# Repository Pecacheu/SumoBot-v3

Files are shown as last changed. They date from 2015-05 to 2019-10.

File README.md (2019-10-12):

# SumoBot 3.0
Everything you need to build a SumoBot!

## Links:
1. Arduino Software at: www.arduino.cc/main/software
2. DCCduino USB-to-Serial chip driver: www.wch.cn/download/CH341SER_EXE.html
3. Mac OS X version: www.wch.cn/download/CH341SER_MAC_ZIP.html
4. Node JS: www.nodejs.org

After installing the DCCduino driver on Mac OS X 10.9 and higher, an extra terminal command may be necessary.
Open Terminal, enter **sudo nvram boot-args="kext-dev-mode=1"**, and hit return.

## SumoBot v3 Assembly Guide:
(Video guide coming soon!)
###### If you're using the acrylic (0.22in) version, determine if you want a cloudy robot or a clear robot. If it's the latter, peel the cloudy protector film off the pieces before use.

#### Side Pieces:
1. Press x-shape inserts onto servo shafts and screw down using black screw.
2. Squeeze black rubber spacers into upper 2 side slots on servo casing.
3. Insert servos into servo holes in side pieces, ensuring that they face in opposite directions.
4. Use 2 silver screws each to secure servos onto side pieces. Add rubber bands to wheels.
6. Attach wheels using 2 silver screws with black rubber spacers (or metal silver spacers) each.

#### Bottom Piece:
6. Screw caster wheel onto bottom piece using remaining 2 black screws. Ensure it's on the opposite side of the piece from the arrow.

#### Chassis Assembly:
7. Insert top and bottom pieces into one of the side pieces, ensuring that all arrows point towards the front of the robot, and are on the topside (for top and bottom pieces) or inner (for side pieces) face.
8. Add the other side piece to the assembly. It's arrow should also face inwards.
9. Screw Arduino onto top piece using final 2 silver screws. The front left and back right holes will work best with most Arduino boards.

#### Wiring:
###### /* TO BE CONTINUED */

#### Final Steps:
10. Push front bumper onto front of robot.
11. Insert Li-Ion battery. Connect battery terminals to power block.

When robot is not in use, disconnect positive wire from battery side. *(NOT from breadboard power block side!)*

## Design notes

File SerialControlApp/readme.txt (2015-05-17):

This is control software, written in Node.js, for the SumoBot Jr. It allows you to control the robot with your computer's keyboard.

In order to use this software, you will need to install Node.js on your computer. Node.js is a popular real time server-side scripting language, based on Google's JavaScript engine. To download your copy, head over to nodejs.org and press the big green install button.

To run this software after installing Node.js, simply open your computer's terminal application, 'cd' to this folder, and type in "node index.js".

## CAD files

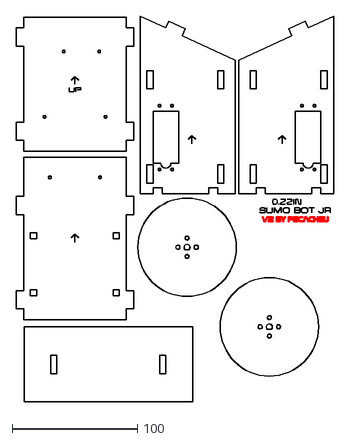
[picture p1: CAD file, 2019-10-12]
Laser Cut Files/0.22in-servos.dxf
253.4 x 307.7

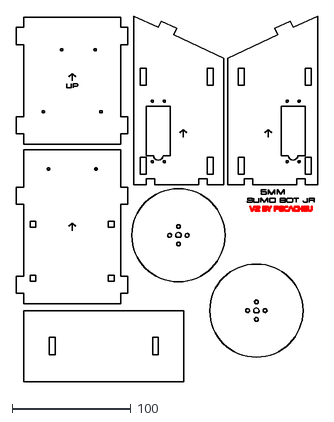
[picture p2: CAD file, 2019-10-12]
Laser Cut Files/5mm-servos.dxf
253.4 x 307.7

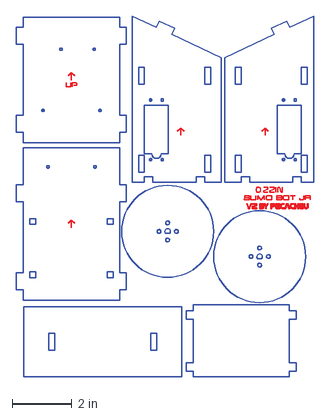
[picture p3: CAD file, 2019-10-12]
Laser Cut Files/sumobot-0.22in.dxf
9.98 x 12.1 in

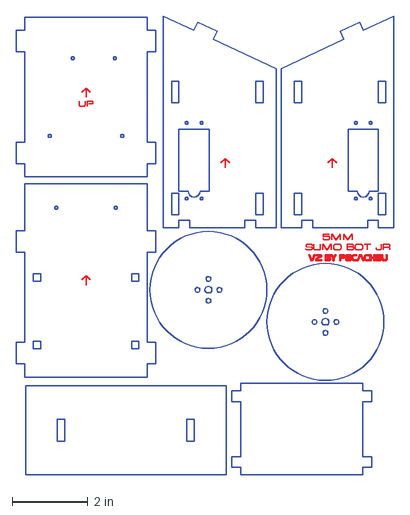
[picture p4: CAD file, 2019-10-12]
Laser Cut Files/sumobot-5mm.dxf
9.98 x 12.1 in

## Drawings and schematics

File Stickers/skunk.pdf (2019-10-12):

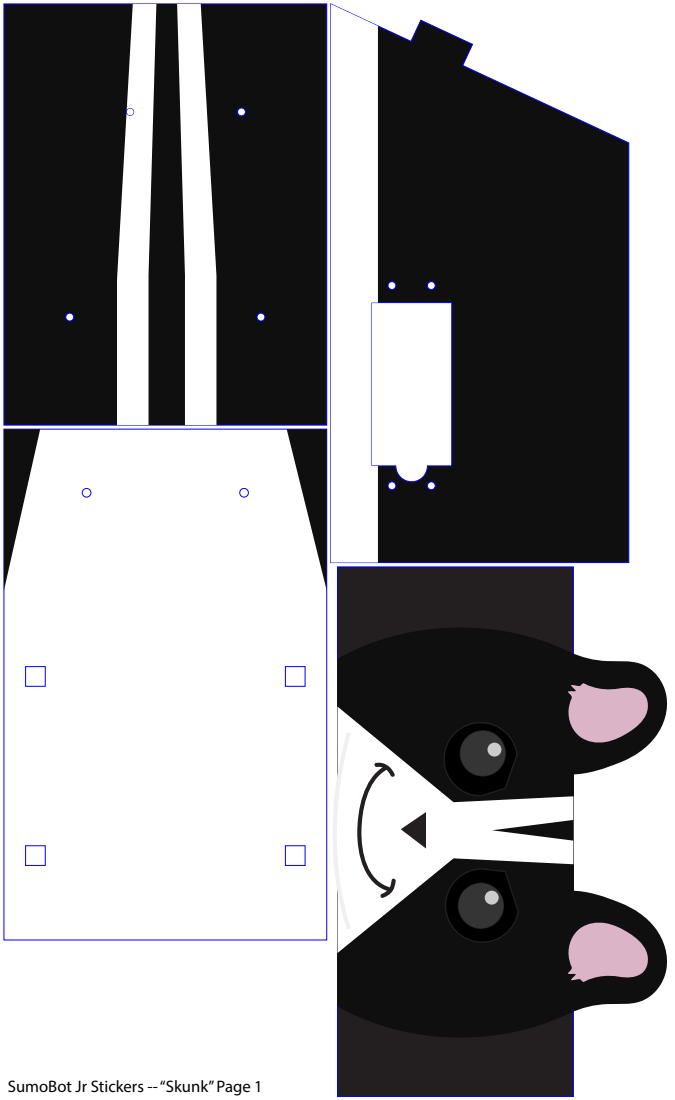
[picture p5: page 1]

SumoBot Jr Stickers -- “Skunk” Page 1

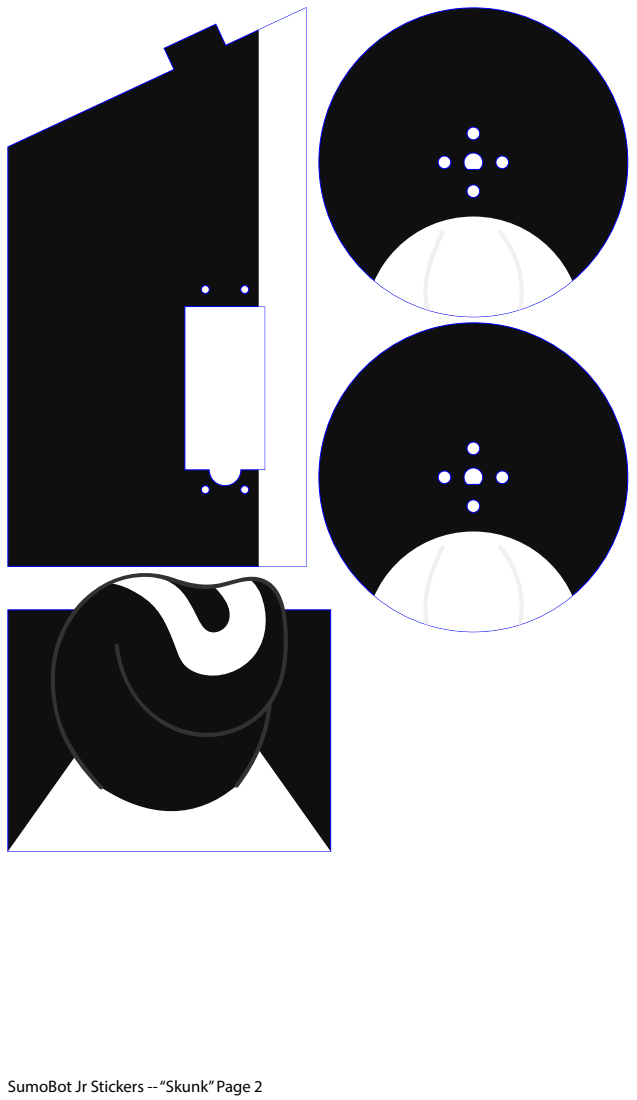
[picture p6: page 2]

SumoBot Jr Stickers -- “Skunk” Page 2

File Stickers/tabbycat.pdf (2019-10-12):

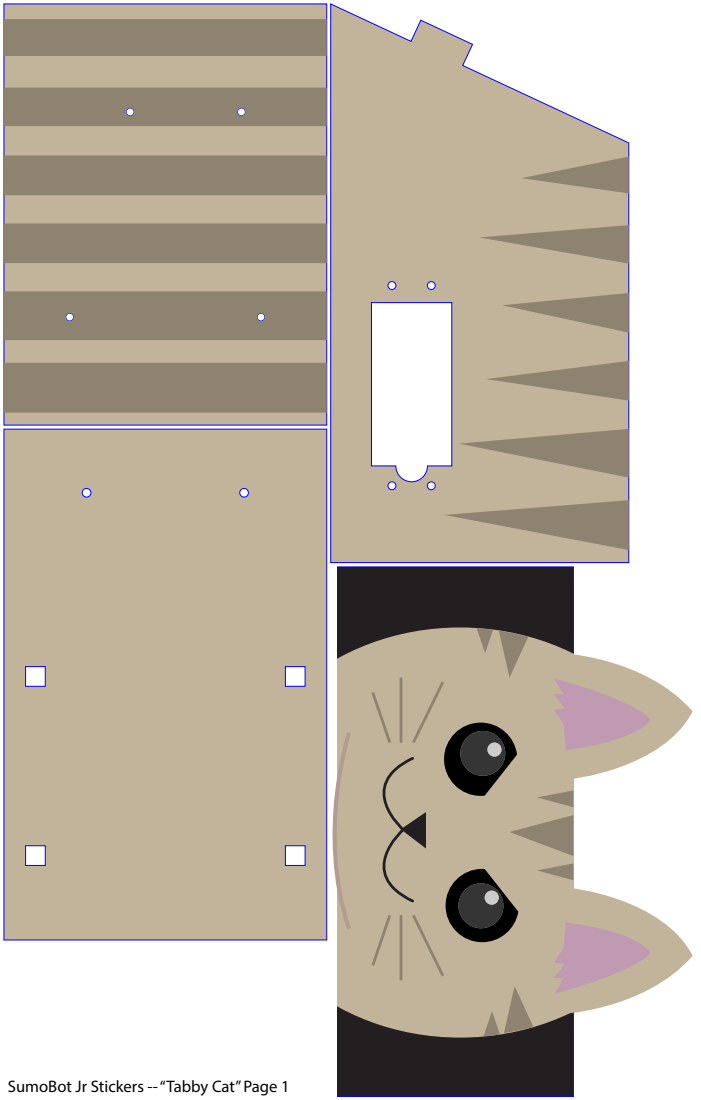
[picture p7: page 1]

SumoBot Jr Stickers -- “Tabby Cat” Page 1

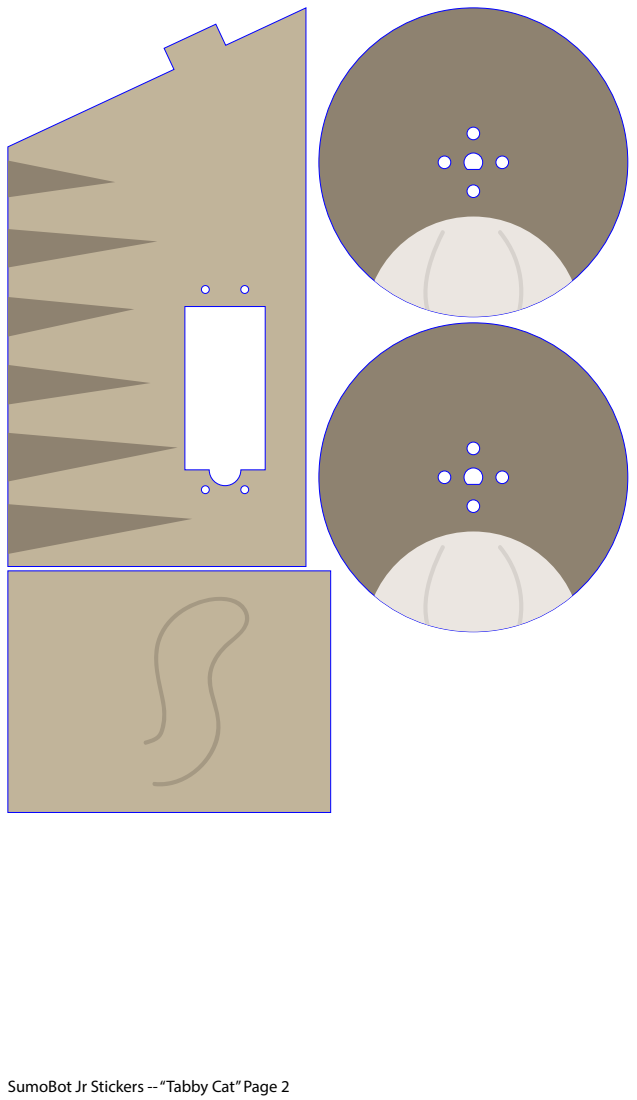
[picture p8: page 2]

SumoBot Jr Stickers -- “Tabby Cat” Page 2

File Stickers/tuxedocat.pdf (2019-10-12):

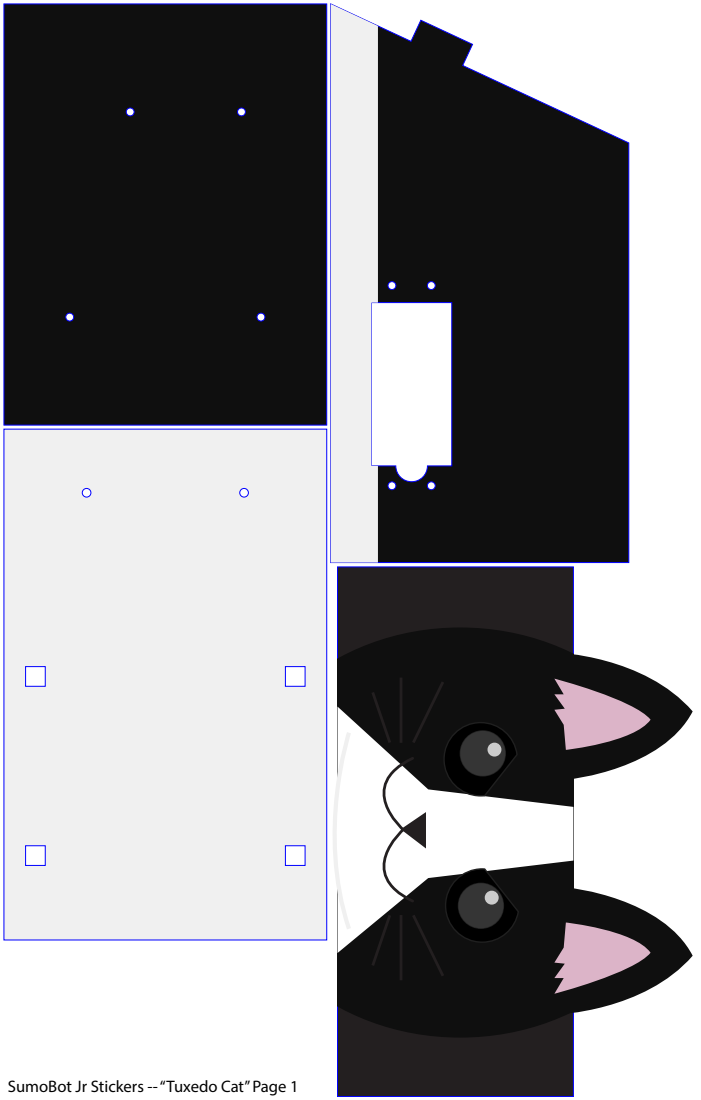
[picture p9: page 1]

SumoBot Jr Stickers -- “Tuxedo Cat” Page 1

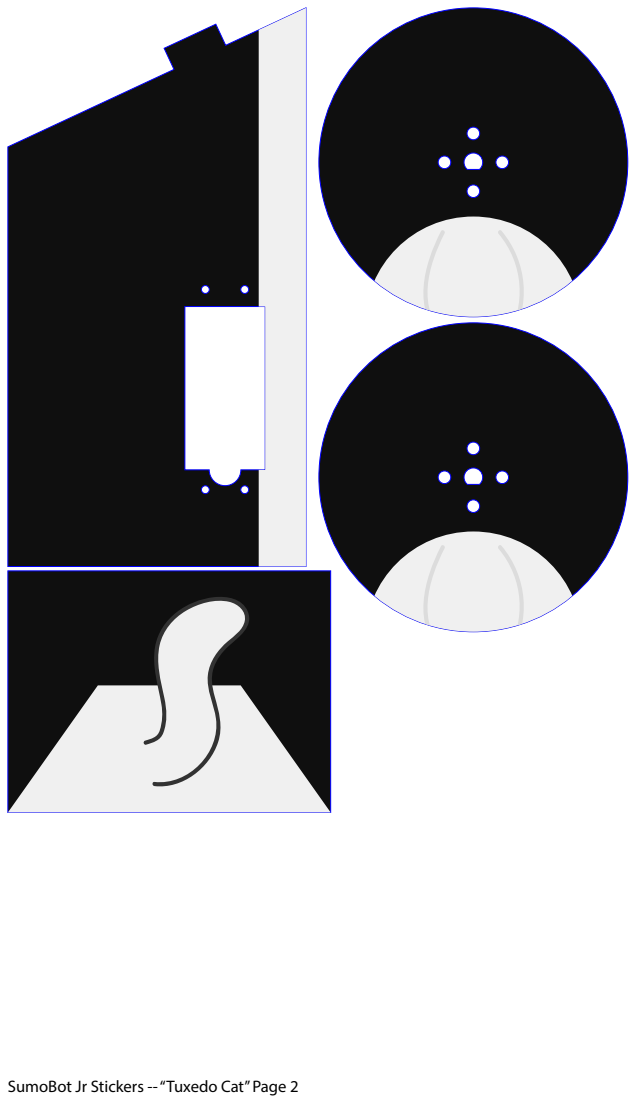
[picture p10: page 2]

SumoBot Jr Stickers -- “Tuxedo Cat” Page 2

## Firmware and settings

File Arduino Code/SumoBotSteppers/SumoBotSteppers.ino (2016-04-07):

//<legalstuff> This work is licensed under a GNU General Public License, v3.0. Visit http://gnu.org/licenses/gpl-3.0-standalone.html for details. </legalstuff>
//SumoBot v3 USB Link (Stepper Version). Copyright (©) 2016, Bryce Peterson (Nickname: Pecacheu, Email: Pecacheu@gmail.com)

//avr-libc library includes:
#include <avr/io.h>
#include <avr/interrupt.h>

#define NUM_MOTORS 2
#define STATUS_LED 13

//Pin Numbers:
#define DIR_1  6
#define STEP_1 5
#define SLP_1  4

#define CONFIG1_M0 3
#define CONFIG1_M1 2

#define DIR_2  10
#define STEP_2 11
#define SLP_2  12

#define CONFIG2_M0 9
#define CONFIG2_M1 8

//Globals: (Don't touch these!)
int savedStepMode = 1;
boolean savedBrakeStates[2] = {true, true};
volatile unsigned int motorPins[2] = {STEP_1, STEP_2};
volatile unsigned int driveMotorSpeed[2] = {0, 0};
volatile unsigned int driveMotorCount[2] = {0, 0};

void setup() {
  //Setup Pins:
  pinMode(STATUS_LED, OUTPUT);
  pinMode(STEP_1, OUTPUT);
  pinMode(DIR_1,  OUTPUT);
  pinMode(SLP_1, OUTPUT);
  digitalWrite(SLP_1, HIGH);
  pinMode(STEP_2, OUTPUT);
  pinMode(DIR_2,  OUTPUT);
  pinMode(SLP_2, OUTPUT);
  digitalWrite(SLP_2, HIGH);
  pinMode(CONFIG1_M0, OUTPUT);
  pinMode(CONFIG1_M1, OUTPUT);
  pinMode(CONFIG2_M0, OUTPUT);
  pinMode(CONFIG2_M1, OUTPUT);
  setStepMode(1); //Set Drivers to Full-Step Mode
  //Init Serial Comm:
  Serial.begin(9600); delay(500);
  //Setup Timer1:
  int timerScale = 1024; int clockSpeed_MHz = 16; int miliSeconds = 1;
  cli(); //Disable Global Interrupts
  TCCR1A = 0; TCCR1B = 0; //Set Entire TCCR1 Register to 0
  TCCR1B |= (1 << CS10); TCCR1B |= (1 << CS12); //Set to 1024 Scale Mode
  //Do The Math:
  double clockPeriod = clockSpeed_MHz*pow(10, 3) / timerScale;
  unsigned int timerCounts = (miliSeconds * clockPeriod) - 1;
  OCR1A = timerCounts; //Set Compare-Match Register to Desired Timer Count
  TCCR1B |= (1 << WGM12); //Turn on CTC Mode
  TIMSK1 |= (1 << OCIE1A); //Enable Timer Compare Interrupt
  sei(); //Enable Global Interrupts
}

void loop() {
  String msg = ""; boolean msgDone = false;
  while(1) {
    //Read New Commands From Serial:
    while(Serial.available() > 0) {
      char newChar = Serial.read();
      //Serial.print((unsigned char)newChar); Serial.print(" = '"); Serial.write(newChar); Serial.println("'"); //<< DEBUG
      if(newChar == '\n') { msgDone = true; break; }
      else msg += newChar;
    }
    
    //Process Next Command:
    if(msgDone && msg.length() >= 1) {
      Serial.print("Data: [");
      for(int i=0; i<msg.length(); i++) { if(i > 0) Serial.print(", "); Serial.print((unsigned char)msg[i]); }
      Serial.print("], Event Type: ");
      if(msg[0] == 'K' && msg.length() == 3) { //Key Update Event:
        Serial.println("Key Update");
        char LEFT = msg[1]; char RIGHT = msg[2];
        if(LEFT == 0) {
          driveMotor(2, false, 1, false);
        } else if(LEFT > 0) {
          driveMotor(2, true, -(abs(LEFT)*2)+256, false);
        } else {
          driveMotor(2, true, -(abs(LEFT)*2)+256, true);
        }
        if(RIGHT == 0) {
          driveMotor(1, false, 1, false);
        } else if(RIGHT > 0) {
          driveMotor(1, true, -(abs(RIGHT)*2)+256, true);
        } else {
          driveMotor(1, true, -(abs(RIGHT)*2)+256, false);
        }
      } else { //Unknown Event:
        Serial.println("Unknown");
      }
    }
    
    //Clear Processed Message Data:
    if(msgDone) { msg = ""; msgDone = false; }
  }
}

//An Exclusive-Or Function:
boolean XOR(boolean a, boolean b) {
  return a != b;
}

//Motor Control Functions:
void driveMotor(unsigned int motorNum, boolean startStop, unsigned char motorSpeed, boolean dir) {
  int STEP_PIN; int DIR_PIN;
  if(motorNum == 1) { STEP_PIN = STEP_1; DIR_PIN = DIR_1; } 
  else if(motorNum == 2) { STEP_PIN = STEP_2; DIR_PIN = DIR_2; }
  else return;
  if(startStop && motorSpeed > 0) {
    engageMotor(motorNum);
    digitalWrite(DIR_PIN, dir);
    int updateDelay = -(motorSpeed/4)+64;
    driveMotorSpeed[motorNum-1] = updateDelay;
  } else {
    driveMotorSpeed[motorNum-1] = 0;
    driveMotorCount[motorNum-1] = 0;
  }
}

void stepMotor(unsigned int motorNum, unsigned int steps, boolean dir) {
  int STEP_PIN; int DIR_PIN;
  if(motorNum == 1) { STEP_PIN = STEP_1; DIR_PIN = DIR_1; } 
  else if(motorNum == 2) { STEP_PIN = STEP_2; DIR_PIN = DIR_2; }
  else return;
  engageMotor(motorNum);
  digitalWrite(DIR_PIN, dir);
  for(int stp=0; stp<steps; stp++) {
    digitalWrite(STEP_PIN, HIGH);
    delay(5);
    digitalWrite(STEP_PIN, LOW);
    delay(5);
  }
}

void disengageMotor(unsigned int motorNum) {
  int SLP_PIN;
  if(motorNum == 1) { SLP_PIN = SLP_1; } 
  else if(motorNum == 2) { SLP_PIN = SLP_2; }
  else return;
  if(savedBrakeStates[motorNum-1]) {
    digitalWrite(SLP_PIN, LOW);
    //pinMode(SLP_PIN, INPUT);
    savedBrakeStates[motorNum-1] = false;
  }
}

void engageMotor(unsigned int motorNum) {
  int SLP_PIN;
  if(motorNum == 1) { SLP_PIN = SLP_1; } 
  else if(motorNum == 2) { SLP_PIN = SLP_2; }
  else return;
  if(!savedBrakeStates[motorNum-1]) {
    //pinMode(SLP_PIN, OUTPUT);
    digitalWrite(SLP_PIN, HIGH);
    savedBrakeStates[motorNum-1] = true;
  }
}

//Step Modes for Pololu LV (White) Stepper Driver:
//1  == Full Step
//2  == Half Step
//8  == Eighth Step
//16 == Sixteenth Step
void setStepMode(int stepMode) {
  switch(stepMode) {
    case 2:
      digitalWrite(CONFIG1_M0, HIGH);
      digitalWrite(CONFIG1_M1, LOW);
      digitalWrite(CONFIG2_M0, HIGH);
      digitalWrite(CONFIG2_M1, LOW);
      savedStepMode = 2;
    break;
    case 8:
      digitalWrite(CONFIG1_M0, LOW);
      digitalWrite(CONFIG1_M1, HIGH);
      digitalWrite(CONFIG2_M0, LOW);
      digitalWrite(CONFIG2_M1, HIGH);
      savedStepMode = 8;
    break;
    case 16:
      digitalWrite(CONFIG1_M0, HIGH);
      digitalWrite(CONFIG1_M1, HIGH);
      digitalWrite(CONFIG2_M0, HIGH);
      digitalWrite(CONFIG2_M1, HIGH);
      savedStepMode = 16;
    break;
    default:
      digitalWrite(CONFIG1_M0, LOW);
      digitalWrite(CONFIG1_M1, LOW);
      digitalWrite(CONFIG2_M0, LOW);
      digitalWrite(CONFIG2_M1, LOW);
      savedStepMode = 1;
  }
}

ISR(TIMER1_COMPA_vect) {
  for(int i=0; i<NUM_MOTORS; i++) { if(driveMotorSpeed[i]) {
    driveMotorCount[i]++;
    if(driveMotorCount[i] >= driveMotorSpeed[i]) {
      driveMotorCount[i] = 0;
      digitalWrite(motorPins[i], HIGH);
      delayMicroseconds(100);
      digitalWrite(motorPins[i], LOW);
    }
  }}
}

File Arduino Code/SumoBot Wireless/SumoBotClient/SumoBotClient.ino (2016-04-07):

//<legalstuff> This work is licensed under a GNU General Public License, v3.0. Visit http://gnu.org/licenses/gpl-3.0-standalone.html for details. </legalstuff>
//SumoBot v3 Wireless Client. Copyright (©) 2016, Bryce Peterson (Nickname: Pecacheu, Email: Pecacheu@gmail.com)

#include <Servo.h>
#include "RF24.h"

//#define NUM_MOTORS 2
#define STATUS_LED 13

//Pin Numbers:
#define MOTORL 2
#define MOTORR 3

#define MIN_PULSE 900
#define MAX_PULSE 2100

//Communication channel name:
byte CH[6] = "Node1";

//Globals: (Don't touch these!)
Servo MotorL; Servo MotorR;
RF24 radio(8,9);

void setup() {
  //Setup Pins & Motors:
  pinMode(STATUS_LED, OUTPUT);
  MotorL.attach(MOTORL); MotorR.attach(MOTORR);
  driveMotor(1, 128); driveMotor(2, 128);
  //Init Wireless Radio:
  radio.begin(); radio.setPALevel(RF24_PA_MAX);
  radio.openReadingPipe(1, CH); //Serial.begin(9600);
  radio.startListening(); //delay(500);
}

void loop() {
  String msg = ""; boolean msgDone = false;
  while(1) {
    //Read New Commands From Wireless Radio:
    while(radio.available() > 0) {
      char newChar; radio.read(&newChar, sizeof(newChar));
      //Serial.print((byte)newChar); Serial.print(" = '"); Serial.write(newChar); Serial.println("'"); //<< DEBUG
      if(newChar == '\n') { msgDone = true; break; }
      else msg += newChar;
    }
    
    //Process Next Command:
    if(msgDone && msg.length() >= 1) {
      //Serial.print("Data: [");
      //for(int i=0; i<msg.length(); i++) { if(i > 0) Serial.print(", "); Serial.print((unsigned char)msg[i]); }
      //Serial.print("], Event Type: ");
      if(msg[0] == 'K' && msg.length() == 3) { //Key Update Event:
        //Serial.println("Key Update");
        byte LEFT = 255-msg[1]; byte RIGHT = msg[2];
        driveMotor(1, LEFT); driveMotor(2, RIGHT);
      } else { //Unknown Event:
        //Serial.println("Unknown");
      }
    }
    
    //Clear Processed Message Data:
    if(msgDone) { msg = ""; msgDone = false; }
  }
}

//Motor Control Functions:
void driveMotor(unsigned int motorNum, byte power) {
  Servo SERVO; if(motorNum == 1) SERVO = MotorL;
  else if(motorNum == 2) SERVO = MotorR; else return;
  if(power == 128) SERVO.writeMicroseconds((MAX_PULSE+MIN_PULSE)/2);
  else SERVO.writeMicroseconds(floor((double(power)/255*(MAX_PULSE-MIN_PULSE))+MIN_PULSE));
}

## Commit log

2015-05-18 Added Automatic Installer
    Also: Added Better Web Interface, Fixed Debug Mode Not Working, Fixed
    Communication Bugs, Added Incoming Data Interpreter / Parser, Fixed
    Arduino Not Turning, Fixed Page Scroll When Arrow Keys Pressed Issue
    [SumoRobotJr_v2_Key_Control.ino, server.js]
2015-05-18 Added Laser Cut Files
    Also: Corrected HTML File Indentation
    [sumbotjr-v2-5mm.dxf]
2015-05-29 Gamepad Support, Complete Interface Redesign!
    Lots of bug-fixes too. Tested in Chrome and Firefox on Mac OS X and
    Windows.
    [SumoBotJrV2_Key_Control.ino, SumoBotJrV2_TEST.ino, server.js]
2015-05-31 Serial Bug Fixes
    +New data protocol for more stable communication.
    *Select port by name or line number.
    *Fixed scroll issues.
    *Arrow keys no longer change scroll position.
    +New advanced auto-installer for offline use.
    [SumoBotJrV2_Key_Control.ino, server.js]
2015-06-02 Even Better Serial
    This new and improved serial protocol sends all key update data in
    whole frames. It should improve reliability and speed.
2015-07-08 Joypad / Joystick Input
    + Faster Serial Protocol
    * Fixed Gamepad Interpretation Code
    [SumoBotJrV2_Key_Control.ino, server.js]
2016-02-28 Servo Support!
    This one’s a BIG update:
    + New Arduino Code Just for Servos
    + New Laser-cut Files with Servo Edition
    + Added Alternate Joystick Mode
    * Updated AutoLoader Version
    * Updated Pecacheu Webserver
    * Code Adjustments and Fixes
    [sumbotjr-v2-5mm.dxf, sumobotjr-v2-servos.dxf, sumobotjr-v2-steppers.dxf]
2016-03-21 Fixed Laser Cutter Files
    [sumobotjr-v2-servos.dxf, sumobotjr-v2-steppers.dxf]
2016-03-21 Fixed Laser Cutter Files (Again)
    [sumobotjr-v2-servos.dxf, sumobotjr-v2-steppers.dxf]
2016-04-06 Win 10 Compatibility
    * Updated AutoLoader Version, v3.0 fixes issues with Windows 8 & 10.
    * Servo values set to center on boot to help with calibration.
    * Left motor channel is now inverted like it should be.
    [SumoBotJrV2_Servo_Ctrl.ino, server.js]
2016-04-07 SumoBot v3.0!
    + Added code for wireless SumoBot using nRF24L01+ modules.
    + Added laser cut files for .22in acrylic. (5mm version is for wood)
    + Added basic assembly instructions.
    * Improved SumoBot design.
    * Renamed repository and several files.
    * Edited README.
    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
    [sumobotjr-v2-servos.dxf, sumobotjr-v2-steppers.dxf]
2016-04-26 Improved Chassis Design
    + Added guide arrows.
    + Added slots for optional backplate.
    * Fixed servo hole size issue.
    * Decreased size of screw holes in wood (5mm) version.
    [0.22in-servos.dxf, 5mm-servos.dxf]
2019-10-12 Add laser files
